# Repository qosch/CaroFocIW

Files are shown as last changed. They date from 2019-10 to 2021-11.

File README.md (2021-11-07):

# CaroFocIW
A small form factor servo inverter for BLDC motors to be mounted directly to the back of the corresponding motor. Intended use in the autonomous 1:10 scale vehicle Carolinchen XI of the Team CDLC (https://www.team-cdlc.de/, german). Firmware compatible with VESC and the custom firmware of the previous iteration. This repository only contains the hardware design.

## Features:
* Field oriented control with sine commutation
* 3× in phase current measurement with oversampling
* 14bit position encoder
* 16kHz sampling rate and PWM frequency
* JST-GH connector with supply and CAN bus interface

## Main components:
Function | used part
------------ | -------------
Microcontroller | STM32F405RGT6
Gate Driver | TLE7185-1E
Current Sensors | 3× ACS71240KEXBLT-010B3
Encoder | AS5048A
CAN Transceiver | TCAN332
Voltage Regulator | LMR16006YQ3
Power MOSFETs | 6× BSZ013NE2LS5I

## Renderings:

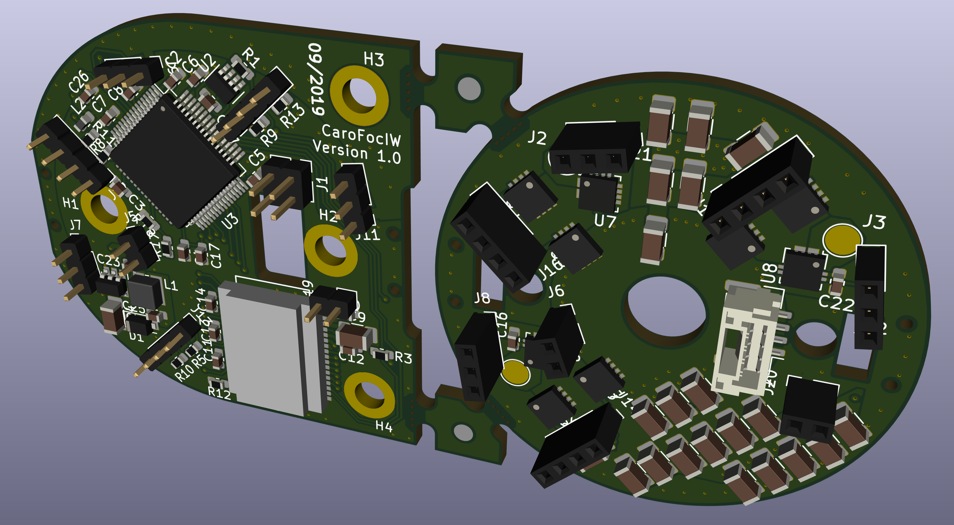
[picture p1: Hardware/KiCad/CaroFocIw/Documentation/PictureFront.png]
PCB Rendering Front


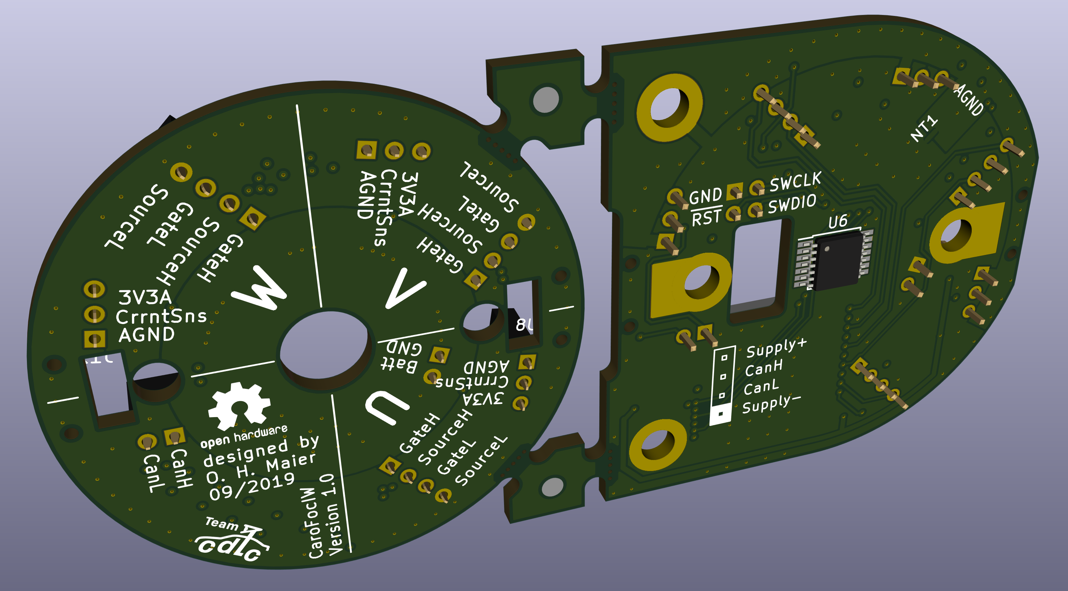
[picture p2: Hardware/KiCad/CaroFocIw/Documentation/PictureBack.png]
PCB Rendering Back


## Progress:
* [x] Schematics finished
* [x] Layout finished
* [x] PCB fabricated
* [x] PCB assembled
* [ ] Mechanical assembly finished
* [x] Basic functional tests done
  * [x] Microcontroller working
  * [x] Gate driver working
  * [x] Current sensors working
  * [x] CAN interface working
  * [x] DC link voltage measurement working
  * [x] Angle encoder working
* [x] Fully operational
* [ ] Tested on vehicle
* [ ] Long term real world testing

Link to [Schematics](https://raw.githubusercontent.com/qosch/CaroFocIW/master/Hardware/KiCad/CaroFocIw/Documentation/Schematics.pdf)

Link to [Interactive BOM](http://htmlpreview.github.io/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)

Link to [PCB assembly and test instructions](https://github.com/qosch/CaroFocIW/blob/master/Hardware/KiCad/CaroFocIw/Documentation/PcbAssemblyAndBasicTests.md)

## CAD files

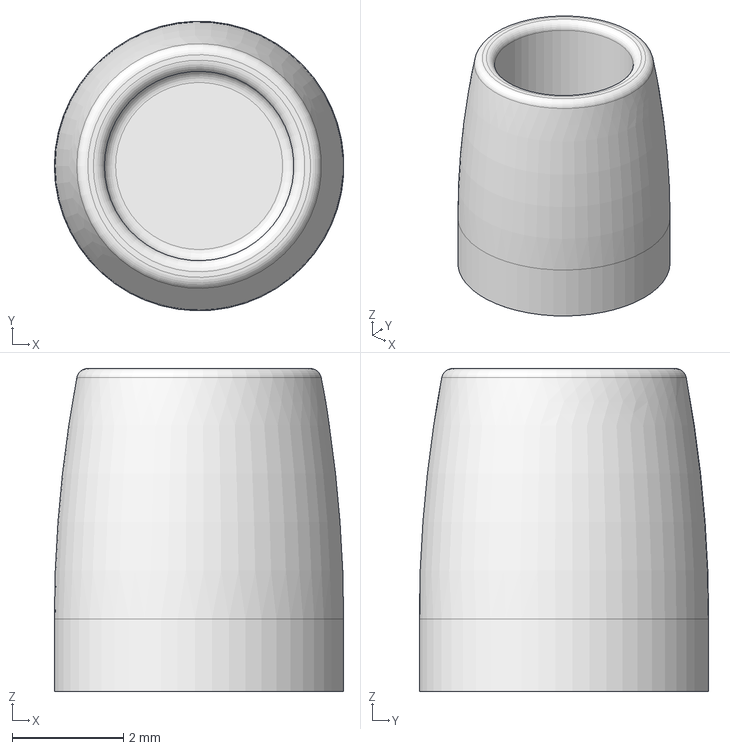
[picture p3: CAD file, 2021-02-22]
Hardware/MCAD/FreeCAD/MagnetHolderD3.4L4.5.FCStd
5.20 x 5.20 x 5.80 mm

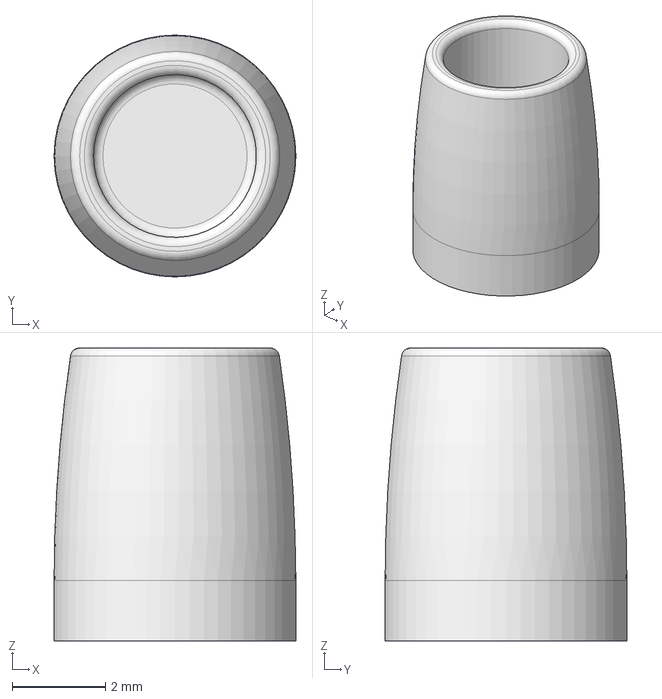
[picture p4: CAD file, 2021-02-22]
Hardware/MCAD/FreeCAD/MagnetHolderD3.5L5.0.FCStd
5.20 x 5.20 x 6.30 mm

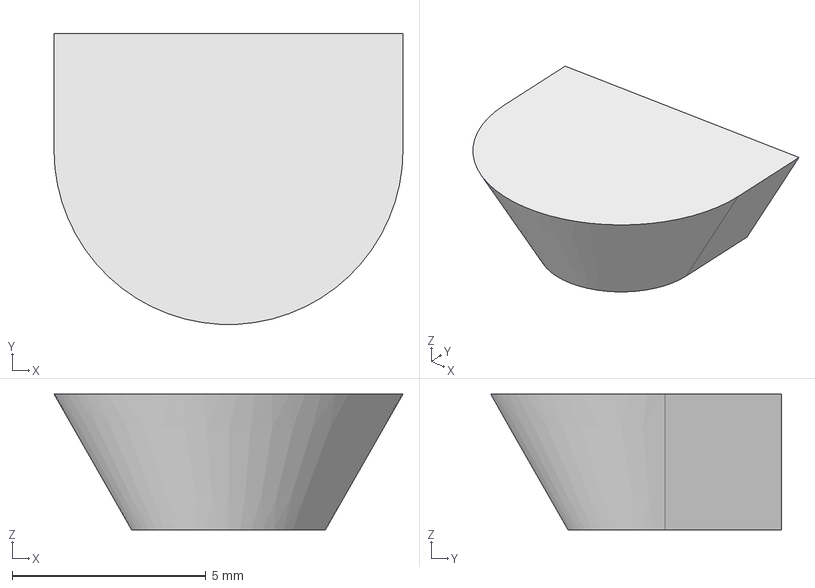
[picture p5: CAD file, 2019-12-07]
Hardware/MCAD/FreeCAD/BallHeadHolder.FCStd
9.00 x 7.49 x 3.50 mm

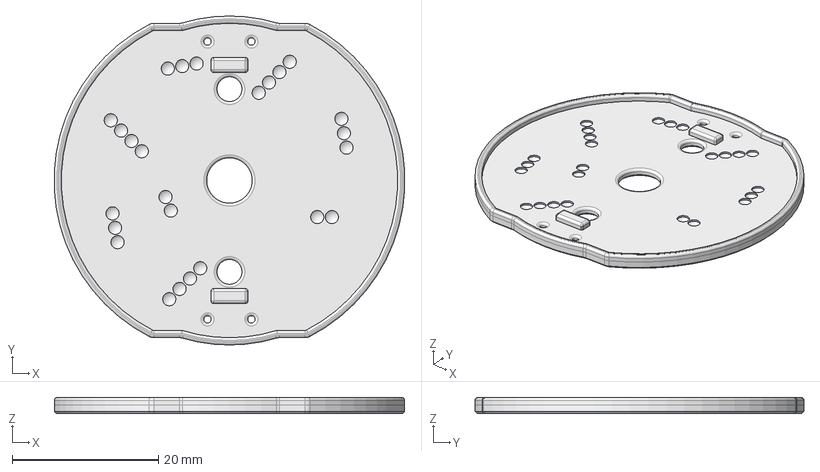
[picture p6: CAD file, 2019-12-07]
Hardware/MCAD/FreeCAD/BackPlateMotor.FCStd
47.9 x 45.0 x 2.20 mm

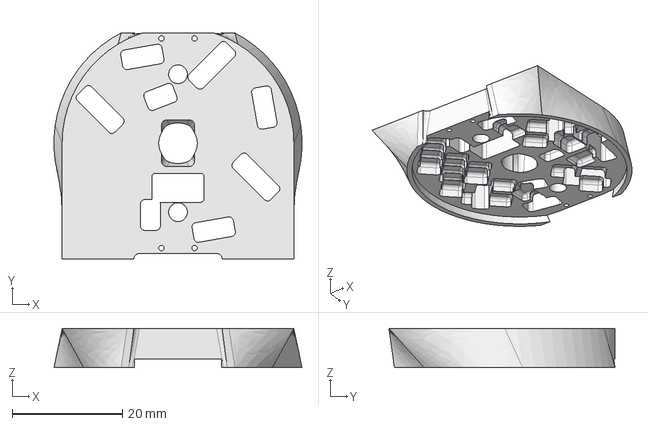
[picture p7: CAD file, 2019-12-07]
Hardware/MCAD/FreeCAD/SpacerPart.FCStd
45.0 x 41.0 x 7.10 mm

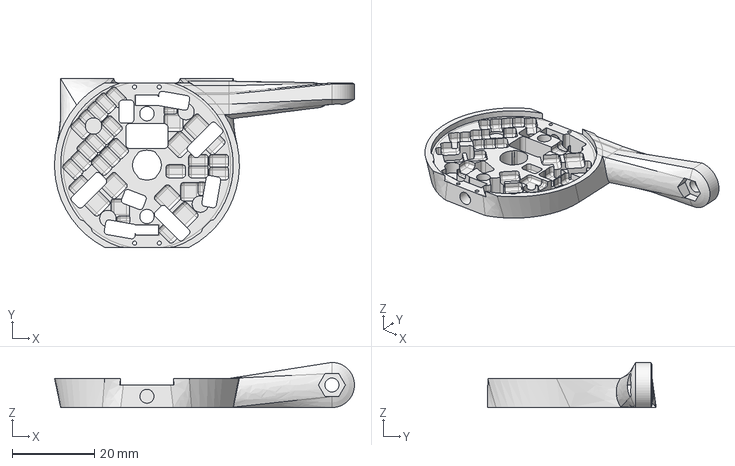
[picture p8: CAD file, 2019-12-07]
Hardware/MCAD/FreeCAD/AnotherTry.FCStd
73.0 x 41.0 x 11.0 mm

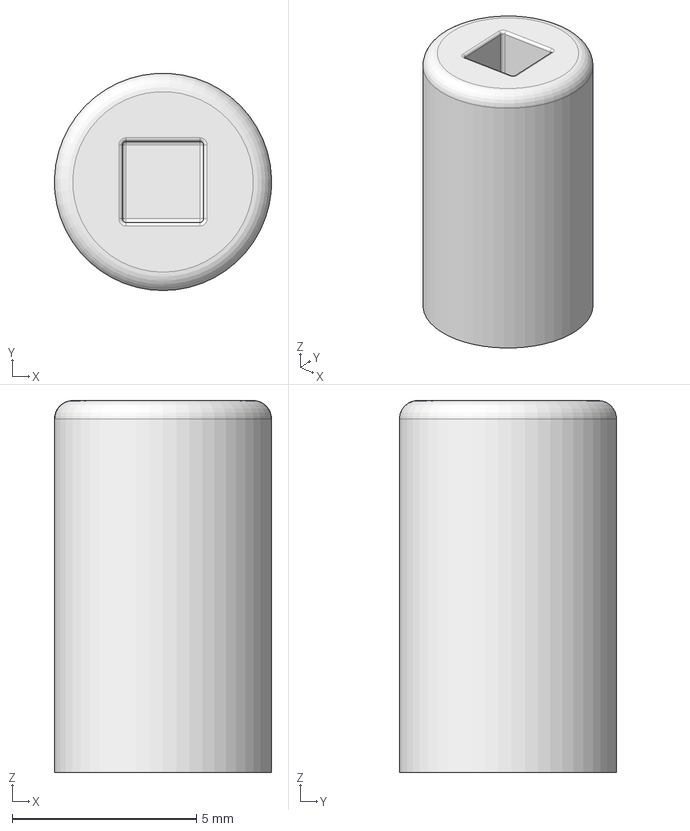
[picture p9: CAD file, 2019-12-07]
Hardware/MCAD/FreeCAD/MagnetHolderCube.FCStd
5.90 x 5.89 x 10.1 mm

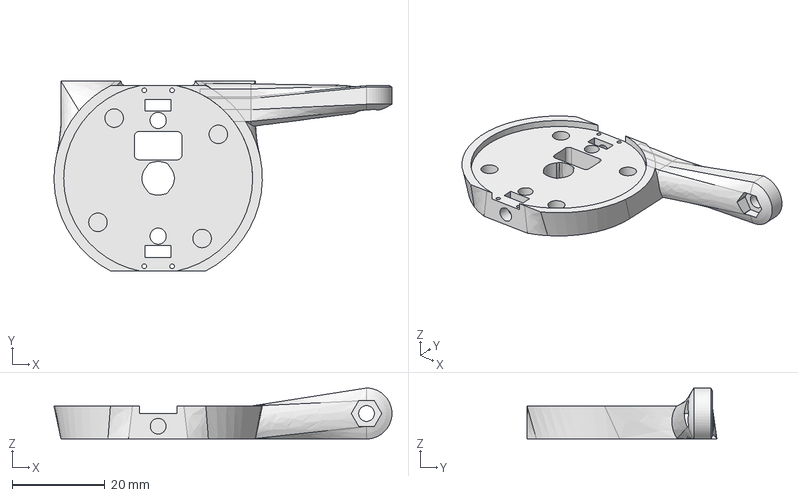
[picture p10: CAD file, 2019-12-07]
Hardware/MCAD/FreeCAD/AnotherTryPCB.FCStd
73.0 x 41.0 x 11.0 mm

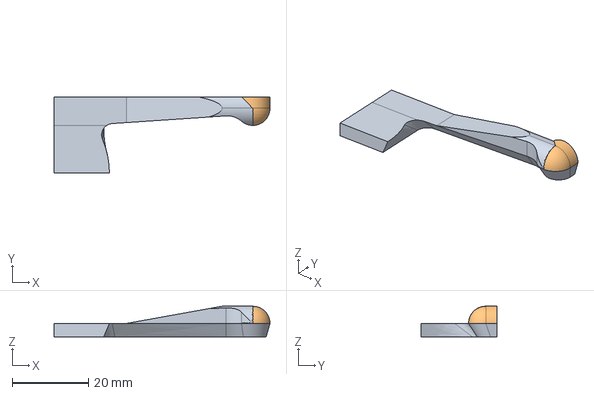
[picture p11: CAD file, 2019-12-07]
Hardware/MCAD/FreeCAD/Spurhebel.FCStd
56.5 x 20.0 x 8.00 mm

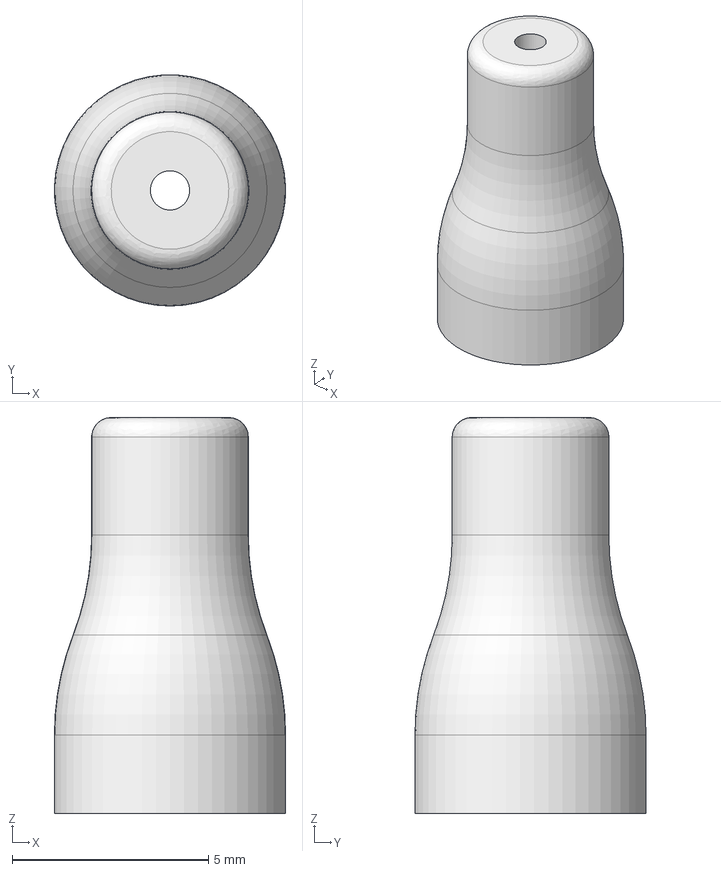
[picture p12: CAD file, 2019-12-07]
Hardware/MCAD/FreeCAD/MagnetHolderRound.FCStd
5.90 x 5.89 x 10.1 mm

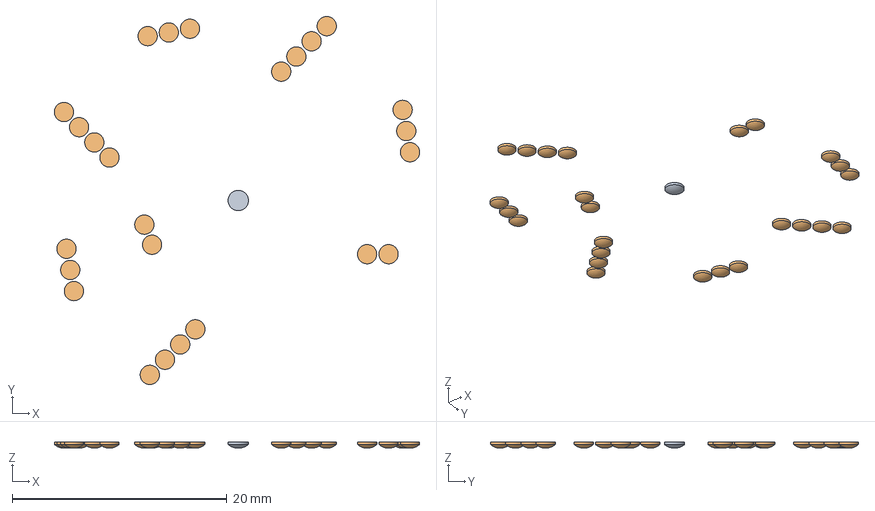
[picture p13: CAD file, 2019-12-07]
Hardware/MCAD/FreeCAD/BackPlateMotorDraft.FCStd
34.0 x 34.3 x 0.6 mm
PointArray

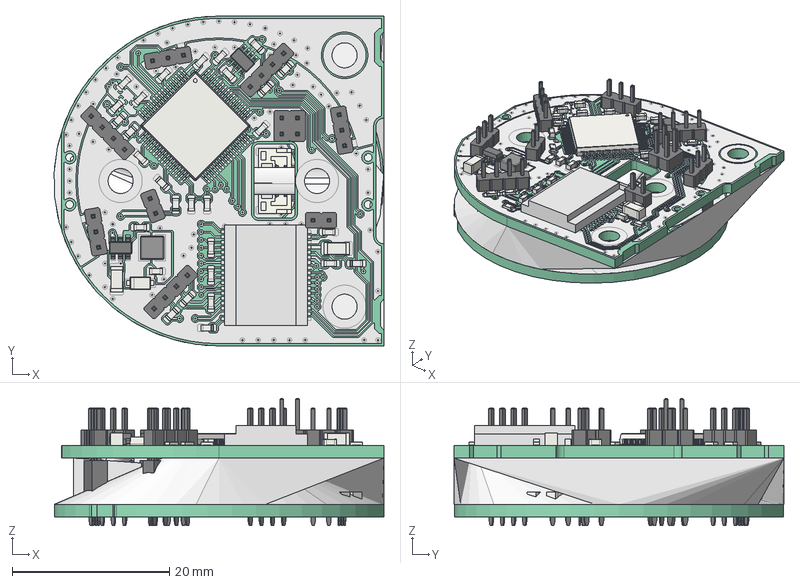
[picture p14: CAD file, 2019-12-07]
Hardware/MCAD/FreeCAD/CaroFocIw.FCStd
42.0 x 42.0 x 16.2 mm
Pcb
topTracks
botTracks
J19_PinHeader_1x02_P200mm_Vertical_5D8CF6D8
J17_PinHeader_1x04_P200mm_Vertical_5D8CF2C3
J15_PinHeader_1x04_P200mm_Vertical_5D8CF1DC
J13_PinHeader_1x04_P200mm_Vertical_5D8CE9C3
J11_PinHeader_1x03_P200mm_Vertical_5D8CF3F4
J9_PinHeader_1x03_P200mm_Vertical_5D8CF220
J7_PinHeader_1x03_P200mm_Vertical_5D8CF658
J5_PinHeader_1x02_P200mm_Vertical_5D8CF699
C4_C_0603_1608Metric_5D8CF1A5
C24_C_1206_3216Metric_5D8CEE63
C9_C_1206_3216Metric_5D8CF28C
U4_Bauteil2_5D8CF5EA
U9_SOT_23_6_5D8CF3B4
U3_LQFP_64_10x10mm_P05mm_5D8CF48A
C13_C_0603_1608Metric_5D8CF59E
C14_C_0603_1608Metric_5D8CF56E
C23_C_0603_1608Metric_5D8CEE93
C25_C_0603_1608Metric_5D8CEEC3
C8_C_0603_1608Metric_5D8CEDA3
C2_C_0603_1608Metric_5D8CEDD3
C3_C_0603_1608Metric_5D8CED43
C6_C_0603_1608Metric_5D8CEE03
C7_C_0603_1608Metric_5D8CEEF3
C12_C_0603_1608Metric_5D8CEC83
C17_C_0603_1608Metric_5D8CEF23
C11_C_0603_1608Metric_5D8CED73
R17_R_0603_1608Metric_5D96668D
R18_R_0603_1608Metric_5D8CECE3
L2_L_0603_1608Metric_5D8CF301
C26_C_0603_1608Metric_5D8CF331
C1_C_0603_1608Metric_5D8CF361
C10_C_0603_1608Metric_5D8CF25C
J1_PinHeader_2x02_P200mm_Vertical_5D8CEA0A
D1_D_SOD_123F_5D8CEFEB
R1_R_0603_1608Metric_5D8CEF53
R3_R_0603_1608Metric_5D8CEFB3
R5_R_0603_1608Metric_5D8CF08B
R8_R_0603_1608Metric_5D8CF0BB
R9_R_0603_1608Metric_5D8CF11B
R10_R_0603_1608Metric_5D8CF14B
R11_R_0603_1608Metric_5D8CEF83
R13_R_0603_1608Metric_5D8CE8C6
L1_L_Wuerth_MAPI_3015_5D8CE866
U2_SOT_23_8_5D8CE8FD
C5_C_0603_1608Metric_5D8CEE33
R12_R_0603_1608Metric_5D8FD4B1
U6_TSSOP_14_44x5mm_P065mm_5D76B81A
Pcb001
topTracks001
botTracks001
J20_PinSocket_1x02_P200mm_Vertical_5C70101C
J18_PinSocket_1x04_P200mm_Vertical_5C6EB429
J16_PinSocket_1x04_P200mm_Vertical_5C6EB411
J14_PinSocket_1x04_P200mm_Vertical_5C6ED233
J12_PinSocket_1x03_P200mm_Vertical_5D752D2D
J10_PinSocket_1x03_P200mm_Vertical_5C705940
J8_PinSocket_1x03_P200mm_Vertical_5C7059AF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

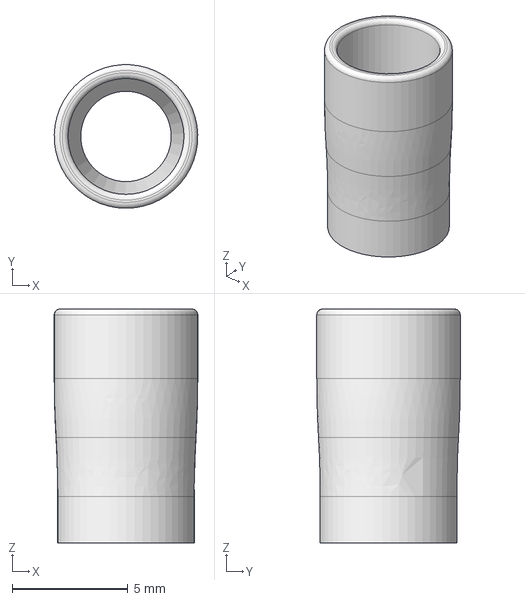
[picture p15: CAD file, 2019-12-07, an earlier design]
Hardware/MCAD/FreeCAD/MagnetHolderOld.FCStd
6.20 x 6.19 x 10.1 mm

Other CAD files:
Hardware/MCAD/FreeCAD/MagnetHolderD3.6L5.5.FCStd

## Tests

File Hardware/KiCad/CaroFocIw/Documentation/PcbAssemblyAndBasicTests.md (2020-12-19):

# Instructions for PCB assembly and tests:

1. Assemble SMT components on top side using a reflow oven.
    1. Make sure you have all neccessary components for the reflow process (go through the BOM), the process cannot be interrupted and resumed later.
    1. Apply solder paste using stencil
    1. Place all SMT components, make sure to align pin 1 correctly for ICs and polarized components. Remerks concerning individual parts:
       1. R1 is the CAN bus termination and only needs to be placed for bus participants close to each end for a linear bus (see [this link](https://www.ni.com/en-us/innovations/white-papers/09/can-physical-layer-and-termination-guide.html) for details, for example).
       1. U3 (STM32 microcontroller) has multiple dots that look like pin 1 markings. The correct one is the smaller one of the two. It is the lower left corner of the package when rotated such that the device marking text can be read.
       1. Q1-Q6 special care should be taken that enough solder paste is present at the gate pin (pin 2).
       1. J4 can be reflow soldered without issues.
    1. Reflow.
    1. Manual inspection and rework. The procedure in the next step will only find the most glaring soldering issues. It is important that most bugs are found before that by manual optical inspection and fixed afterwards.
1. Check for most common soldering issues using a multimeter:
    1. PCB A
       1. tbc
    1. PCB B
       1. J14, J16, J18: Measure capacitance between all neighbouring pins (so 9 measurements in total). Expected result: 1nF-5nF
       1. J8, J10, J12: Measure resistance between pin 1 and pin 2 and between pin 2 and pin 3. Expected result: 100kΩ-1MΩ
       1. J8, J10, J12: Measure resistance between pin 1 and pin 3. Expected result: 20kΩ-200kΩ
       1. J8, J10, J12: Measure resistance between pin 1 and pin 3. Expected result: 20kΩ-200kΩ
       1. All pins of J8, J10, J12 should have a resistance >10MΩ to any pin of any other connector on this PCB (except for the pins of the same connector). Check J8<->J14+J6, J10<->J16+J6, J12<->J18+J6.
       1. Pin 1 and 2 of J20 should only have connection to pins 2 and 3 of J4. Check J20<->J6 (all 4 combinations). Expected result: >10MΩ
       1. J6: Measure capacitance between pin 1 and pin 4. Expected result: 150-250µF
1. Apply power to the individual PCBs.
   1. PCB A: GND -> J5 Pin 1, +3.3V -> J7/J9/J11 pin 3. Set current limit to 50mA and measure supply current. If you want to be extra careful use a 10Ω series resistor. Turn up voltage slowly. With unprogrammed microcontroller suppy current should remain <20mA.
   1. PCB A: GND -> J5 pin 1, +20V -> J5 pin 2. Set current limit to 100mA and measure supply current as well as voltage at J7/J9/J11 pin 3. Turn up voltage slowly. Voltage at J7/J9/J11 pin 3 should remain at 3.2-3.4V as soon as power supply voltage reaches 3.5V. Suppy current should remain <200mA
   1. PCB B: GND -> J6 pin 1 or J4 pin 1, +20V -> J6 Pin 2 or J4 pin 4. Set current limit to 50mA and measure supply current. If you want to be extra careful use a 1kΩ series resistor. Turn up voltage slowly. Suppy current should remain <20mA.
   1. PCB B: Repeat for J8, J10, J12: GND -> pin 1, +3.3V pin 3. Set current limit to 50mA. If you want to be extra careful use a 10Ω series resistor. Turn up voltage slowly. Suppy current should remain <20mA. Measure voltage between pin 1 (GND) and pin 2. Expected voltage: half the supply voltage at pin 3.
1. Solder in U6 using hot air, infrared or soldering iron. Manual inspection and rework. Use a continuity tester to check all pins against GND (J5 pin 1), only pin 13 should be connected. Check all pins against +3.3V (J7/J9/J11 pin 3), only pin 11 and 12 should be connected. Check that pin 1-4 do not have shorts to neighbours. Repeat "Apply power" tests with PCB A.
1. Break apart PCB A and PCB B. The intermediate parts are not needed anymore.
1. Assemble the inter-board-connectors. They are used a bit differently than normal and need to be modified.
   1. Break of parts of the male pin header connector to the neccessary leghts (2× 2 pin, 3× 3 pin, 3x 4 pin).
   1. The black plastic part is not in the right position for our usage, it needs to be pushed down such that the longer part of the pin sticks out even longer. To do that, place an unpopulated PCB on a flat, hard surface, put the shorter side of a pinheader in to the holes and push the plastic down to the PCB.
   1. Insert all modified pin headers into PCB A so that the black plastic part and the very short side of the pins is on the top side.
   1. Put an unpopulated PCB on top so that the pinheaders are held in place when you turn the PCB around.
   1. Solder the connectors in from the bottom side. Use as little solder as possible, only make sure the hole around the pin is filled with solder all around the pin. Try to prevent the solder from flowing up the pin or leaving solder on the upper part of the pin as it will prevent the pin from being fully inserted into the female part on PCB B.
   1. Insert the female headers from the top side of PCB B and solder them from the back. Again, try to use as little solder as possible.
   1. Cut the pins on the back of PCB B as short as possible to prevent them from being shorted by the motor's metal case. Make sure no cut off metal parts remain on the PCBs.
1. Assemble programming connector J1 from top, solder from back.
1. Wash PCB A and B to remove remaining flux.
1. Plug PCB A into PCB B and apply power to J6 pin 1 (GND) and pin 4 (+20V). With unprogrammed microcontroller, suppy current should remain <50mA.
1. Connect a programmer to J1 and check connection to the microcontroller using the tool of you choice.
Additional remark: Be very careful when unplugging PCB A from PCB B. The inter-board connectors may break when PCBs are not kept parallel during unplugging.

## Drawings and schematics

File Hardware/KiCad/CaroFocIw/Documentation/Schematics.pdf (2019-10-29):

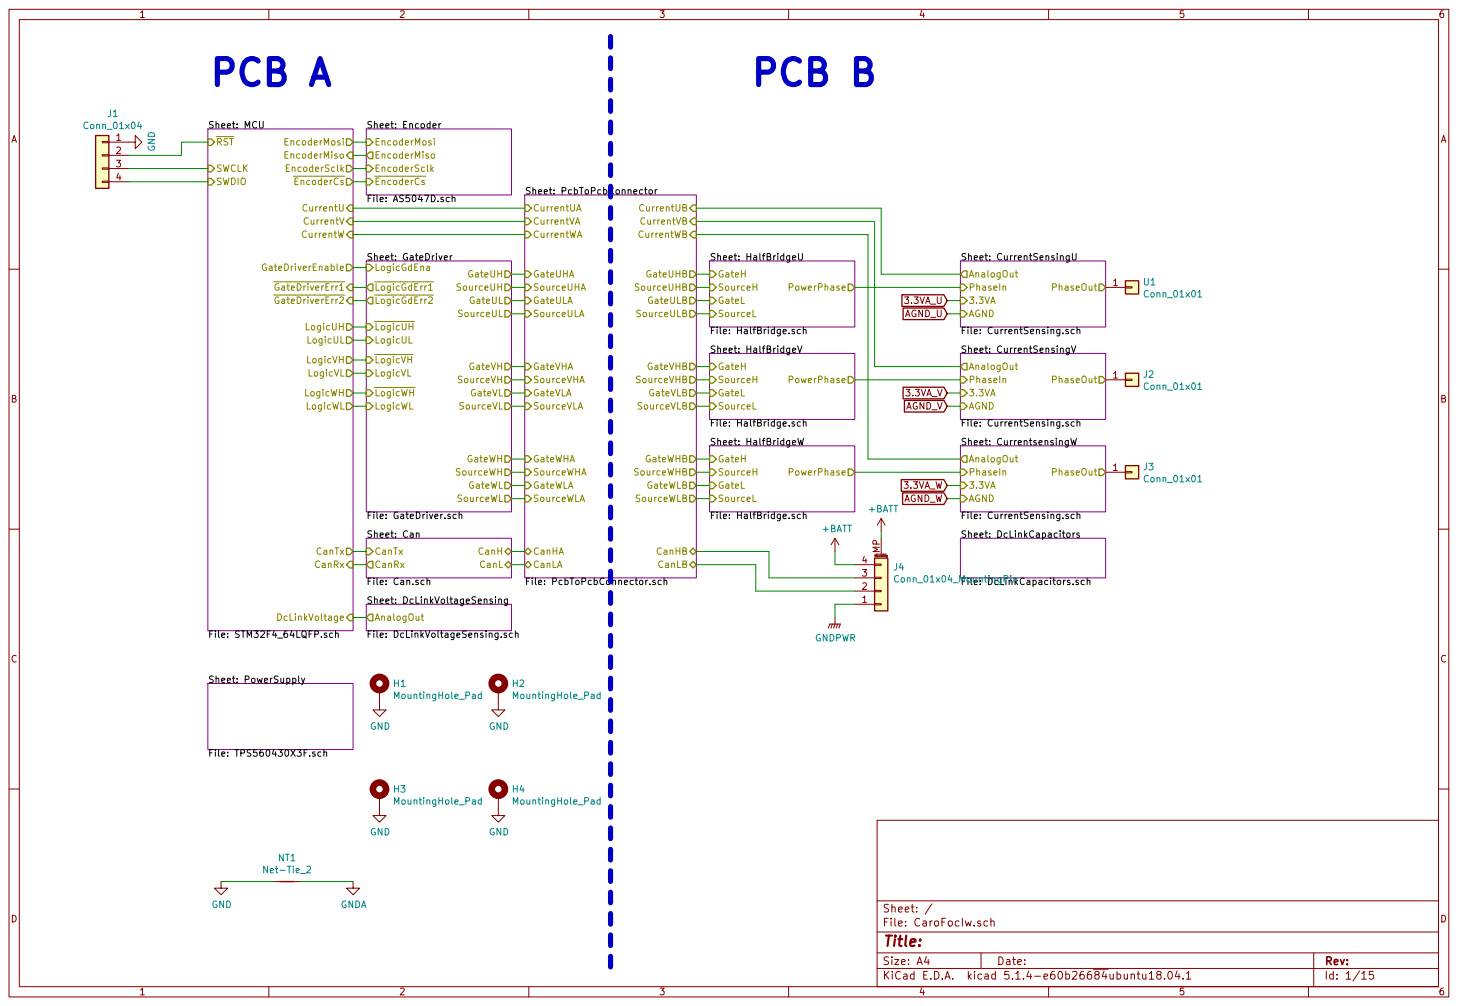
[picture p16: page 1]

LogicWL EncoderSclk EncoderMiso EncoderMosi EncoderCs GateDriverEnable GateDriverErr1 GateDriverErr2 SWDIO
File: STM32F4_64LQFP.schCanRx CanTx CurrentU

Sheet: HalfBridgeU
File: HalfBridge.sch PowerPhase GateH GateL SourceL SourceH

LogicGdEna
SourceUL SourceVL SourceWL GateWL GateVL GateUL GateWH GateVH GateUH

Sheet: HalfBridgeV

Id: 1/15 Title: File: CaroFocIw.sch Sheet: / Sheet: DcLinkVoltageSensing
AnalogOut
File: DcLinkVoltageSensing.sch

Sheet: PowerSupply File: TPS560430X3F.sch

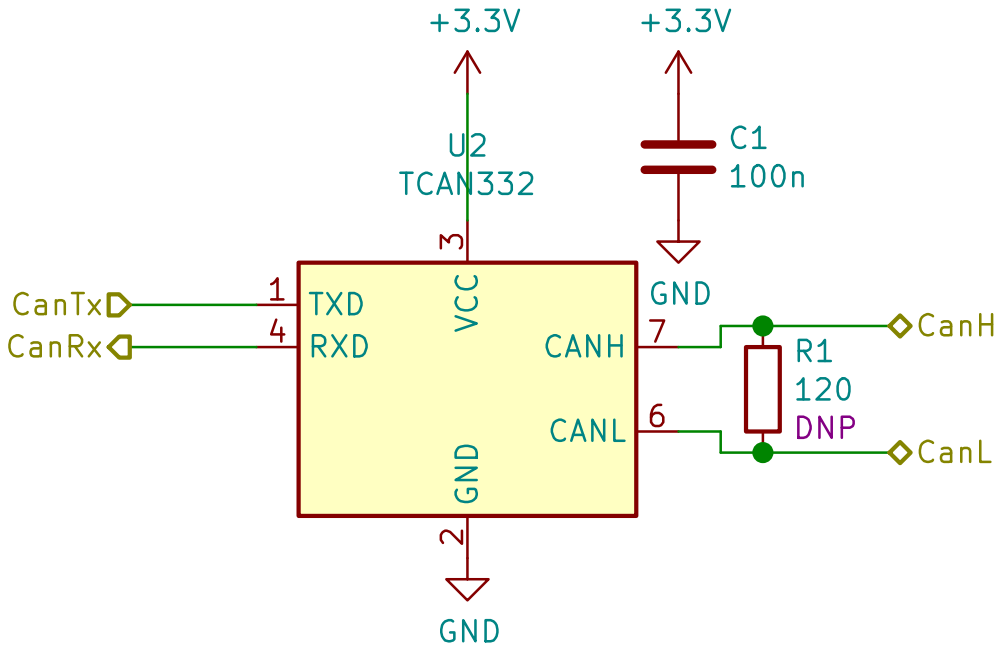
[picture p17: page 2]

3 RXD 4 CANL 6 CANH 7 U2 TCAN332 CanRx CanL CanH CanTx

Id: 2/15 Title: File: Can.sch Sheet: /Can/ R1

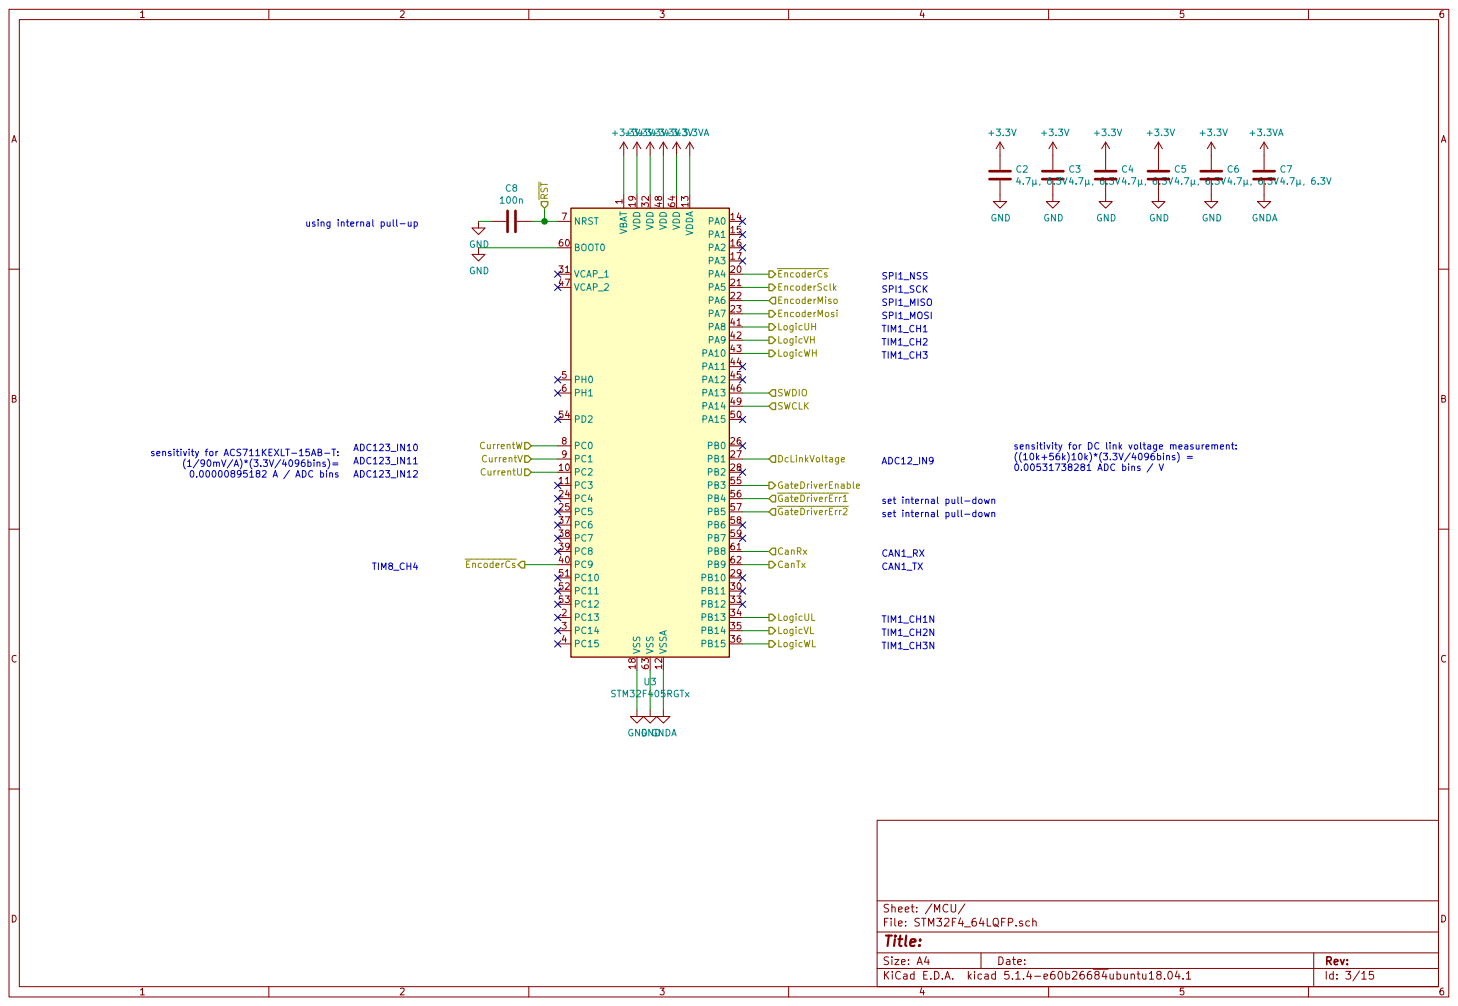
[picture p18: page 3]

1 VCAP_1 31 VCAP_2 47 VDD 19 VDD 32 VDD 48 VDD 64 VDDA 13 VSS 18 VSS 63 VSSA 12 U3 STM32F405RGTx

using internal pull-up

CanTx GateDriverErr2 EncoderCs EncoderMosi EncoderMiso ADC123_IN12 TIM8_CH4

LogicWL EncoderSclk GateDriverEnable CurrentU

sensitivity for DC link voltage measurement:
((10k+56k)10k)*(3.3V/4096bins) =
0.00531738281 ADC bins / V

set internal pull-down
set internal pull-down TIM1_CH1N

File: STM32F4_64LQFP.sch Sheet: /MCU/
Id: 3/15 Title:

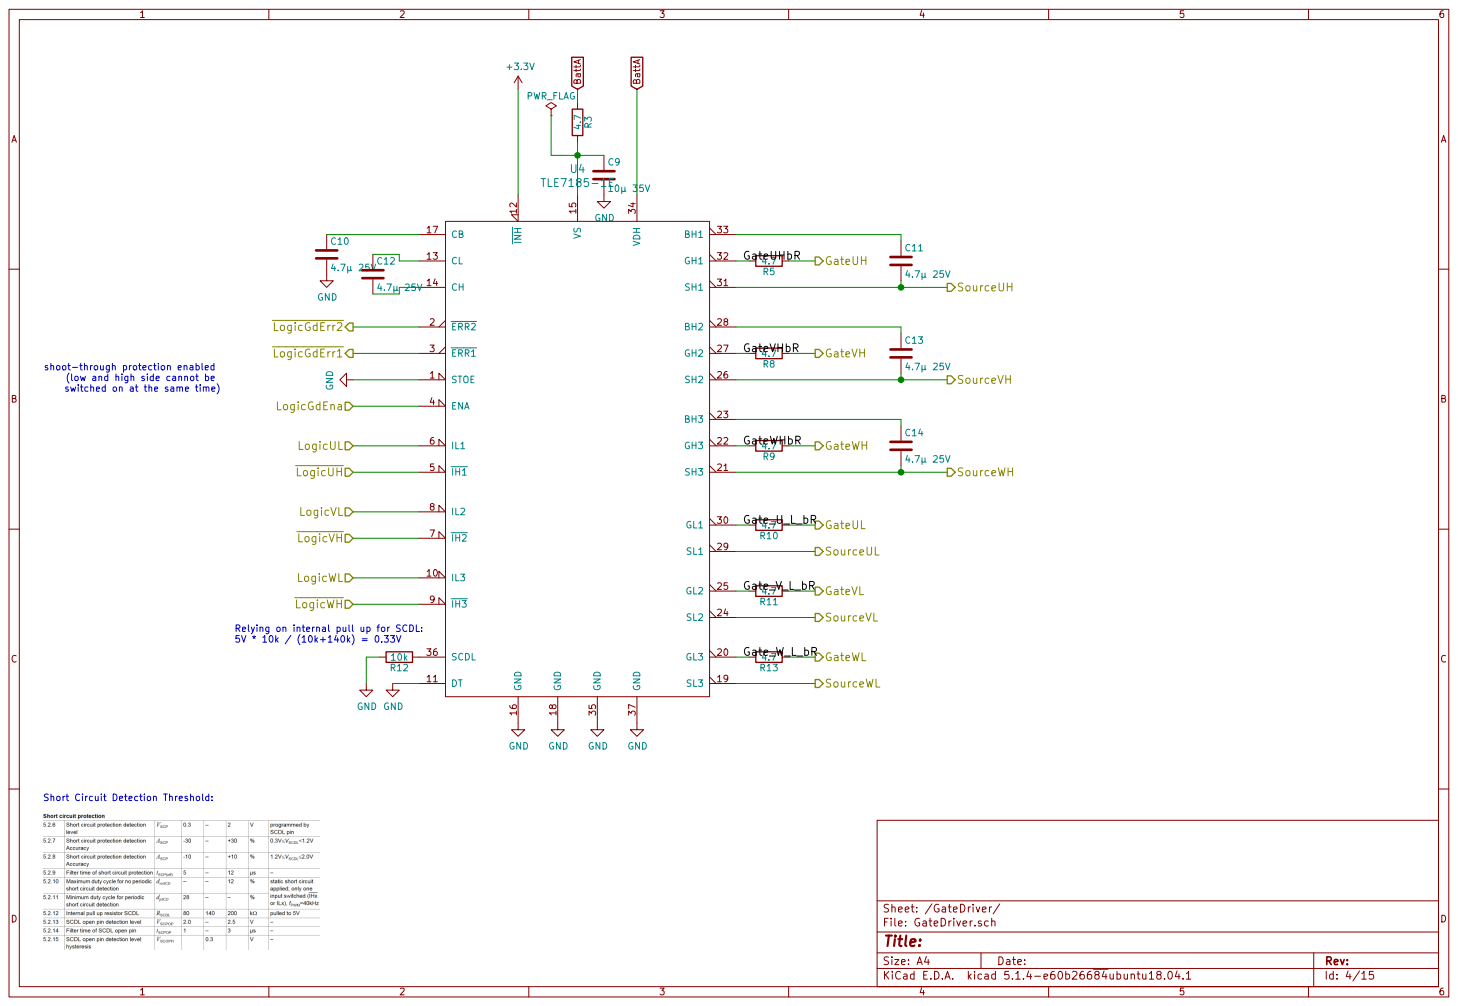
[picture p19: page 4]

shoot-through protection enabled
(low and high side cannot be
switched on at the same time)

Relying on internal pull up for SCDL:

Id: 4/15 Title: File: GateDriver.sch Sheet: /GateDriver/ R12

Short Circuit Detection Threshold:

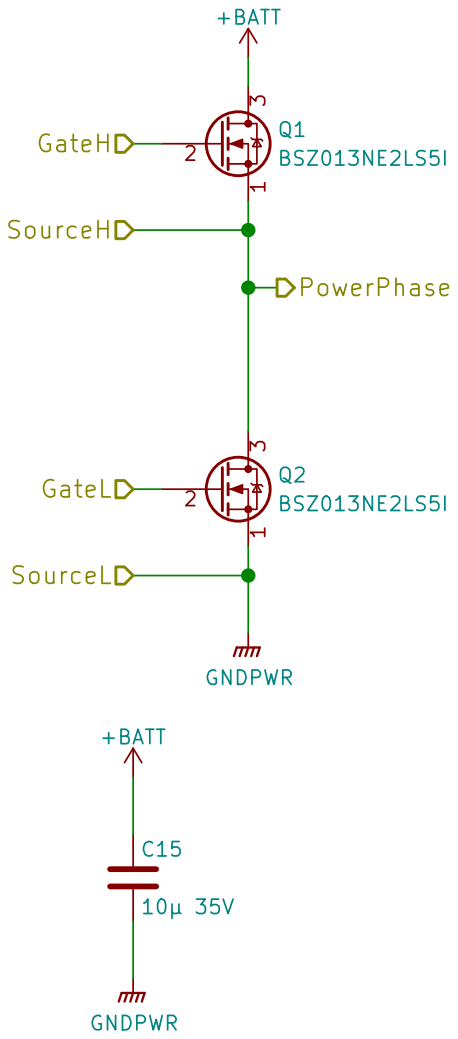
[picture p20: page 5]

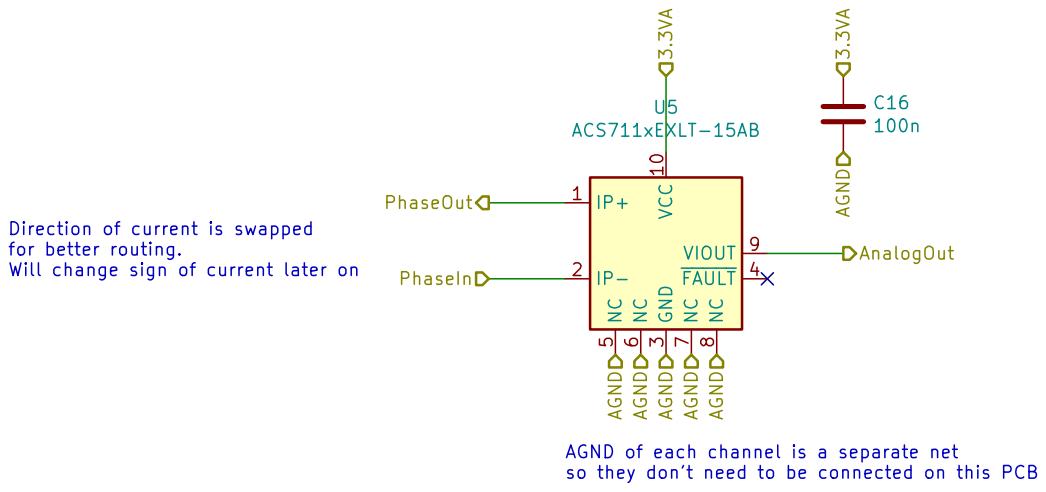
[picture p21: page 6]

AnalogOut PhaseIn Direction of current is swapped
for better routing.
Will change sign of current later on

AGND of each channel is a separate net
so they don't need to be connected on this PCB

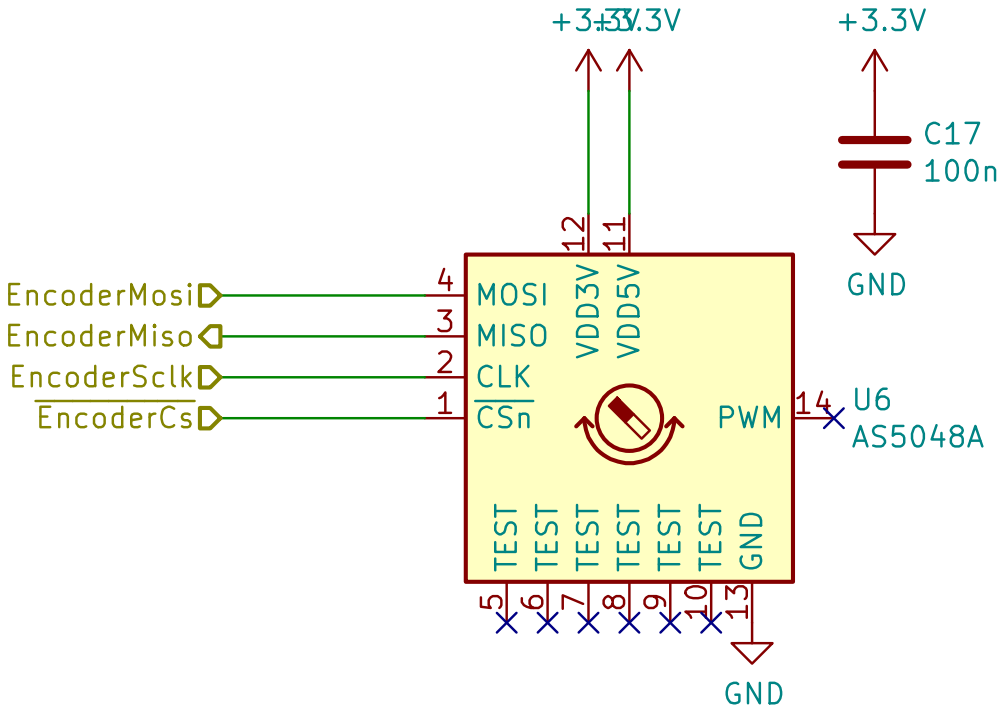
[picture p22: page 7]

100n EncoderMosi EncoderCs EncoderSclk EncoderMiso

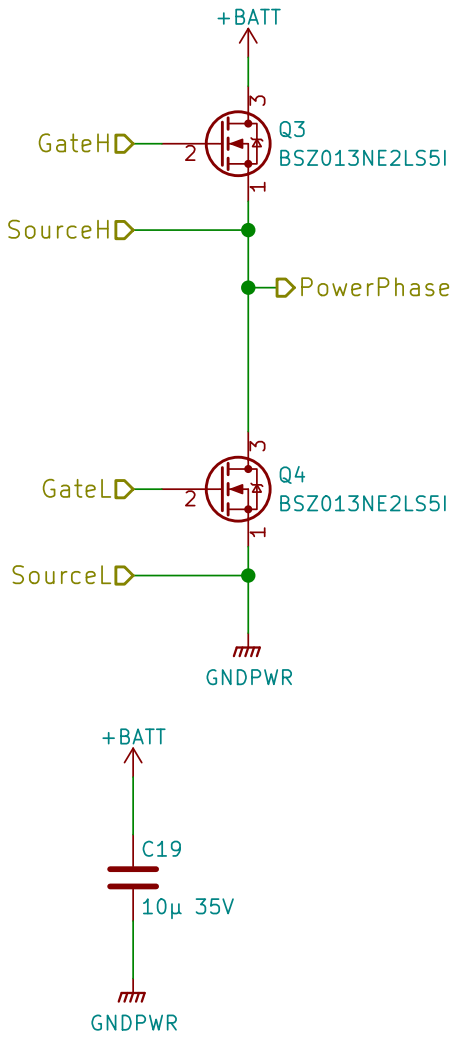
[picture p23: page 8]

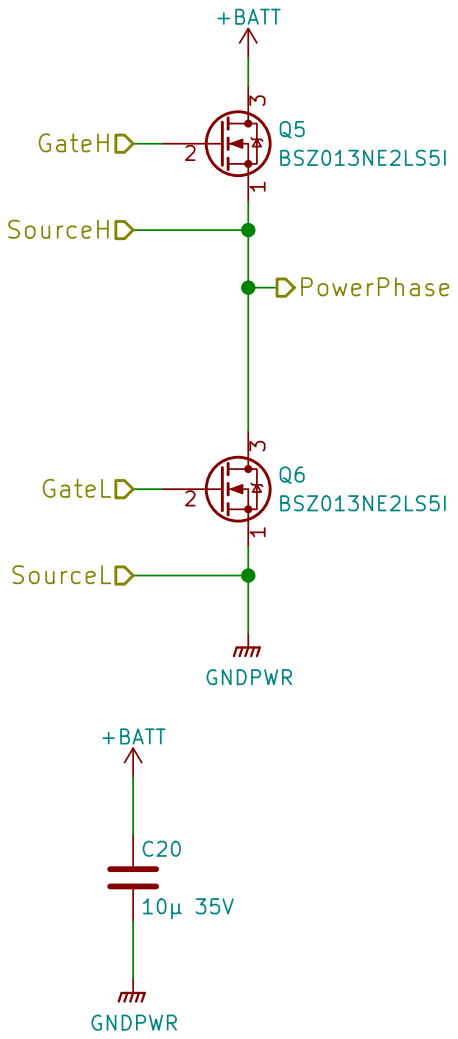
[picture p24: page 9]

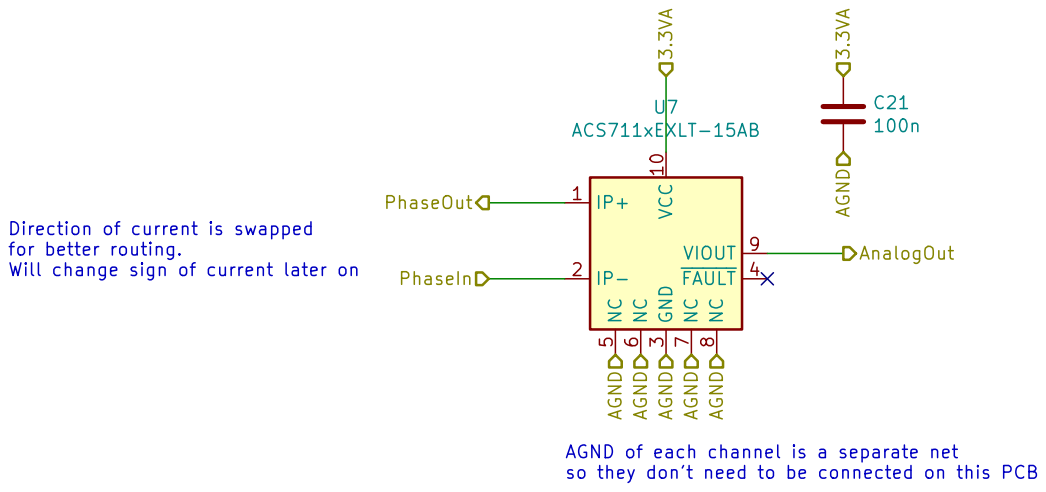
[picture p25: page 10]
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

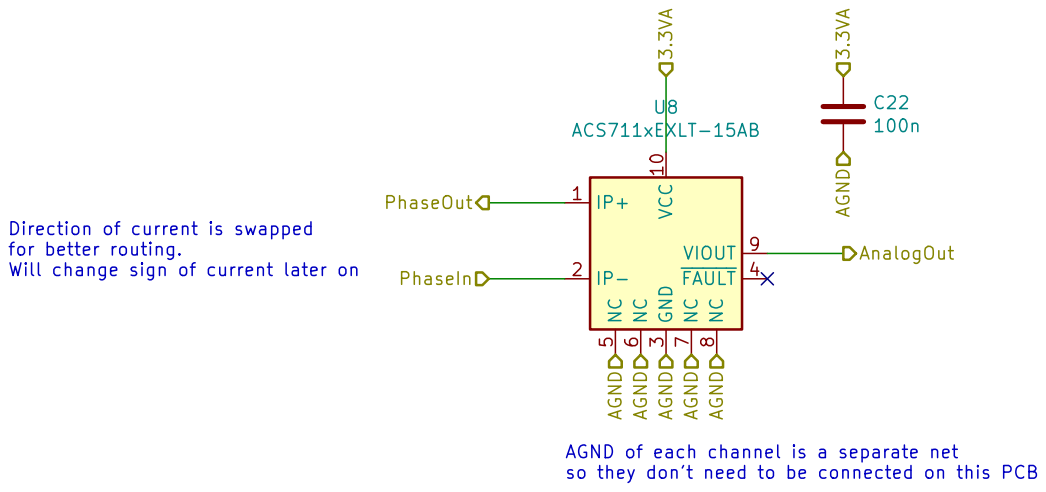
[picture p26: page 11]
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

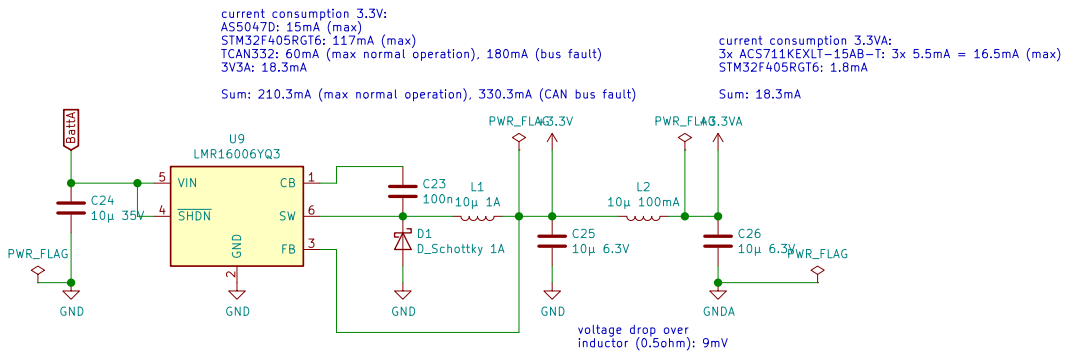
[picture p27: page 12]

current consumption 3.3V:
AS5047D: 15mA (max)
STM32F405RGT6: 117mA (max)
TCAN332: 60mA (max normal operation), 180mA (bus fault) 3V3A: 18.3mA

Sum: 210.3mA (max normal operation), 330.3mA (CAN bus fault)

2 FB 3 SHDN 4 VIN 5 SW 6 U9

Id: 12/15 Title: File: TPS560430X3F.sch Sheet: /PowerSupply/


+BATT GNDPWR GNDA GNDA GNDA

AGND and 3.3VA of each channel don't need to be connected on PCB B

(they are connected on PCB A)

Id: 13/15 Title: File: PcbToPcbConnector.sch Sheet: /PcbToPcbConnector/


outputs 3.3V for 21.78V Battery voltage



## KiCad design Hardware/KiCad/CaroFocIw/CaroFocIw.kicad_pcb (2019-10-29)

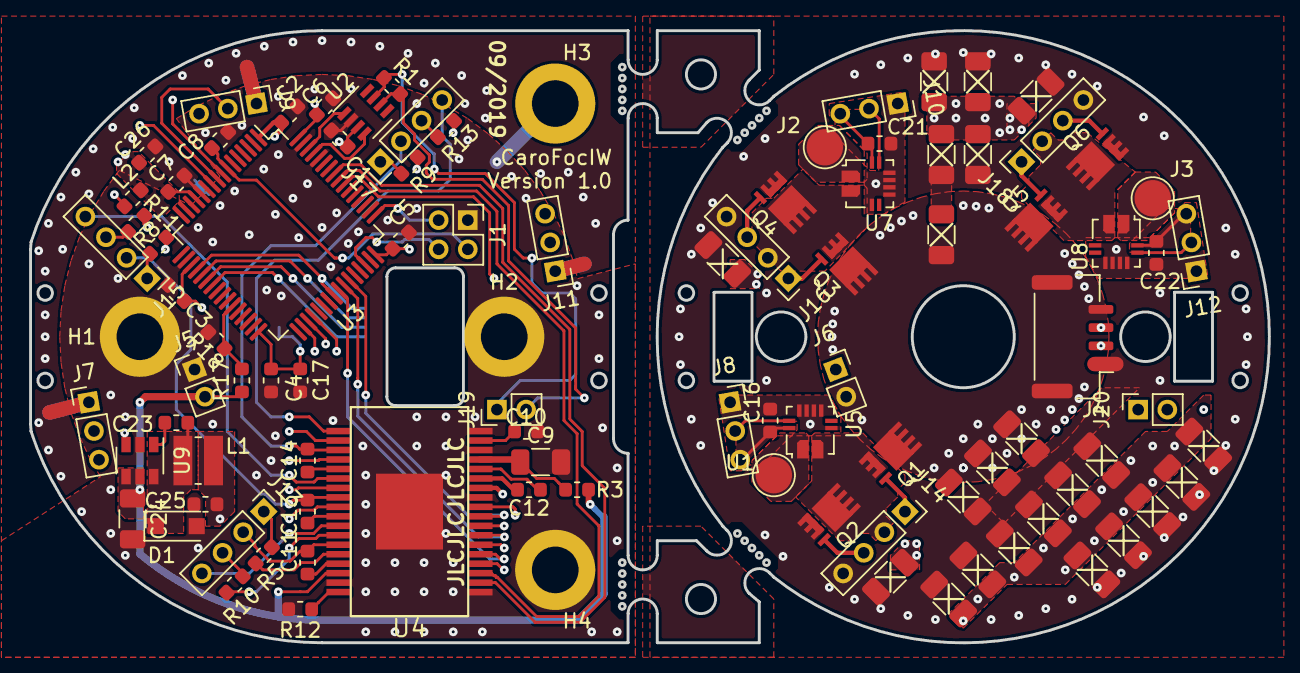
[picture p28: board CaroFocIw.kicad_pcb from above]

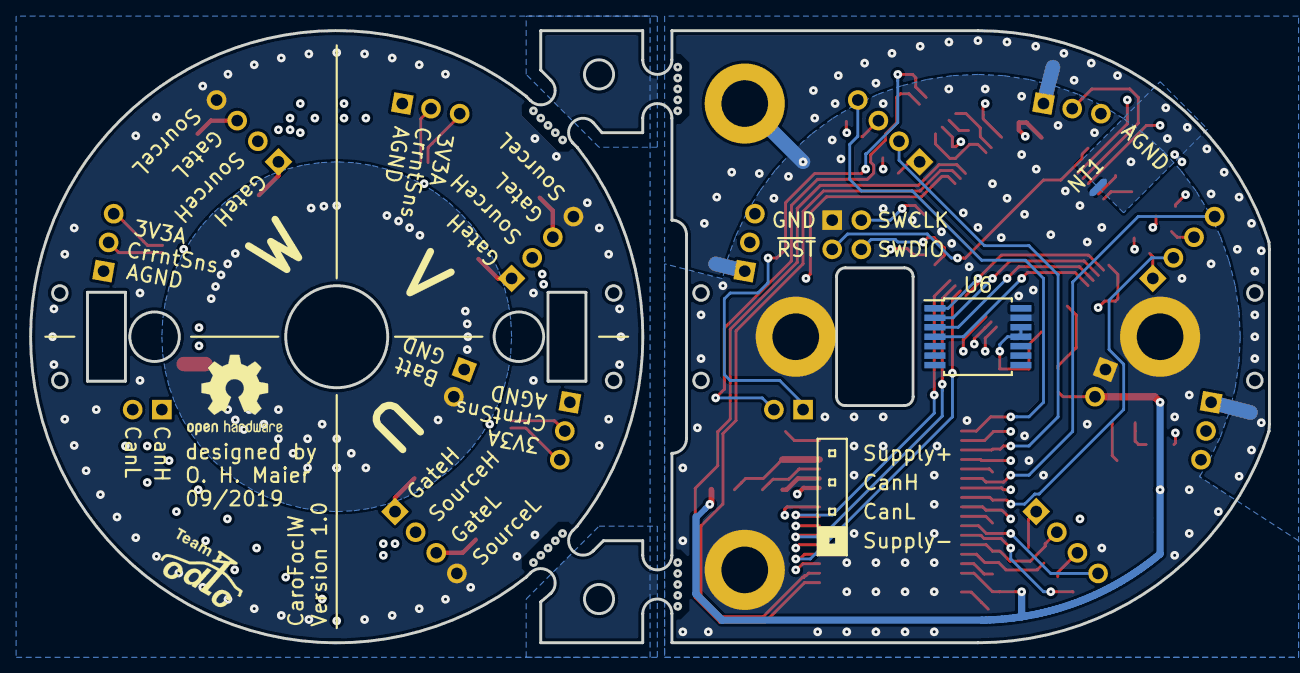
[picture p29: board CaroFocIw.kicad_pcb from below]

Board: 4 copper layers, 85.0 x 42.0 mm, 98 parts (2 on the bottom side), 82 nets.

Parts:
C1, C8, C16, C17, C21, C22, C23: 100n; C_0603_1608Metric
C2, C3, C4, C5, C6, C7: 4.7µ, 6.3V; C_0603_1608Metric
C9, C27, C28, C29, C30, C31, C32, C33, C34, C35, C36, C37, C38, C39, C40, C41, C42, C43, C44, C45: 10µ 35V; C_1206_3216Metric
C10, C11, C12, C13, C14: 4.7µ 25V; C_0603_1608Metric
C15, C19, C20, C24: 10μ 35V; C_1206_3216Metric
C25, C26: 10μ 6.3V; C_0603_1608Metric
D1: D_Schottky 1A; D_SOD-123F
H1, H2, H3, H4: MountingHole_Pad; MountingHole_3.2mm_M3_ISO14580_Pad
J1: Conn_01x04; PinHeader_2x02_P2.00mm_Vertical
J2, J3: Conn_01x01; TestPoint_Pad_D2.5mm
J4: Conn_01x04_MountingPin; JST_GH_BM04B-GHS-TBT_1x04-1MP_P1.25mm_Vertical
J5, J19: Conn_01x02; PinHeader_1x02_P2.00mm_Vertical
J6, J20: Conn_01x02; PinSocket_1x02_P2.00mm_Vertical
J7, J9, J11: Conn_01x03; PinHeader_1x03_P2.00mm_Vertical
J8, J10, J12: Conn_01x03; PinSocket_1x03_P2.00mm_Vertical
J13, J15, J17: Conn_01x04; PinHeader_1x04_P2.00mm_Vertical
J14, J16, J18: Conn_01x04; PinSocket_1x04_P2.00mm_Vertical
L1: 10μ 1A; L_Wuerth_MAPI-3015
L2: 10μ 100mA; L_0603_1608Metric
NT1: Net-Tie_2; NetTie-2_SMD_Pad0.5mm
Q1, Q2, Q3, Q4, Q5, Q6: BSZ013NE2LS5I; PG-TSDSON-8-FL
R1: 120; R_0603_1608Metric
R3, R5, R8, R9, R10, R11, R13: 4.7; R_0603_1608Metric
R12, R18: 10k; R_0603_1608Metric
R17: 56k; R_0603_1608Metric
U1: Conn_01x01; TestPoint_Pad_D2.5mm
U2: TCAN332; SOT-23-8
U3: STM32F405RGTx; LQFP-64_10x10mm_P0.5mm
U4: TLE7185-1E; PG-DSO-36-38
U5, U7, U8: ACS711xEXLT-15AB; Allegro_QFN-12-10-1EP_3x3mm_P0.5mm
U6: AS5048A; TSSOP-14_4.4x5mm_P0.65mm
U9: LMR16006YQ3; SOT-23-6

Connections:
3.3VA_U: C16.1, J8.3, U5.10
3.3VA_V: C21.1, J10.3, U7.10
3.3VA_W: C22.1, J12.3, U8.10
+3.3VA: C7.1, C26.1, J7.3, J9.3, J11.3, L2.1, U3.13
+3V3: C1.1, C2.1, C3.1, C4.1, C5.1, C6.1, C17.1, C25.1, L1.1, L2.2, U2.3, U3.1, U3.19, U3.32, U3.48, U3.64, U4.12, U6.11, U6.12, U9.3
+BATT: C15.1, C19.1, C20.1, C27.1, C28.1, C29.1, C30.1, C31.1, C32.1, C33.1, C34.1, C35.1, C36.1, C37.1, C38.1, C39.1, C40.1, C41.1, C42.1, C43.1, C44.1, C45.1, J4.4, J4.MP, J6.2, Q1.3, Q3.3, Q5.3
/Can/CanH: J19.1, R1.1, U2.7
/Can/CanL: J19.2, R1.2, U2.6
/Can/CanRx: U2.4, U3.61
/Can/CanTx: U2.1, U3.62
/CurrentSensingU/AnalogOut: J8.2, U5.9
/CurrentSensingU/PhaseIn: J14.2, Q1.1, Q2.3, U5.2
/CurrentSensingU/PhaseOut: U1.1, U5.1
/CurrentSensingV/AnalogOut: J10.2, U7.9
/CurrentSensingV/PhaseIn: J16.2, Q3.1, Q4.3, U7.2
/CurrentSensingV/PhaseOut: J2.1, U7.1
/CurrentsensingW/AnalogOut: J12.2, U8.9
/CurrentsensingW/PhaseIn: J18.2, Q5.1, Q6.3, U8.2
/CurrentsensingW/PhaseOut: J3.1, U8.1
/DcLinkVoltageSensing/AnalogOut: R17.2, R18.1, U3.27
/Encoder/EncoderMiso: U3.22, U6.3
/Encoder/EncoderMosi: U3.23, U6.4
/Encoder/EncoderSclk: U3.21, U6.2
/Encoder/~EncoderCs: U3.20, U3.40, U6.1
/GateDriver/GateUH: J13.1, R5.1
/GateDriver/GateUHbR: R5.2, U4.32
/GateDriver/GateUL: J13.3, R10.1
/GateDriver/GateVH: J15.1, R8.1
/GateDriver/GateVHbR: R8.2, U4.27
/GateDriver/GateVL: J15.3, R11.1
/GateDriver/GateWH: J17.1, R9.1
/GateDriver/GateWHbR: R9.2, U4.22
/GateDriver/GateWL: J17.3, R13.1
/GateDriver/Gate_U_L_bR: R10.2, U4.30
/GateDriver/Gate_V_L_bR: R11.2, U4.25
/GateDriver/Gate_W_L_bR: R13.2, U4.20
/GateDriver/LogicUL: U3.34, U4.6
/GateDriver/LogicVL: U3.35, U4.8
/GateDriver/LogicWL: U3.36, U4.10
/GateDriver/SourceUH: C11.2, J13.2, U4.31
/GateDriver/SourceUL: J13.4, U4.29
/GateDriver/SourceVH: C13.2, J15.2, U4.26
/GateDriver/SourceVL: J15.4, U4.24
/GateDriver/SourceWH: C14.2, J17.2, U4.21
/GateDriver/SourceWL: J17.4, U4.19
/HalfBridgeU/GateH: J14.1, Q1.2
/HalfBridgeU/GateL: J14.3, Q2.2
/HalfBridgeV/GateH: J16.1, Q3.2
/HalfBridgeV/GateL: J16.3, Q4.2
/HalfBridgeW/GateH: J18.1, Q5.2
/HalfBridgeW/GateL: J18.3, Q6.2
/MCU/CurrentU: J7.2, U3.10
/MCU/CurrentV: J9.2, U3.9
/MCU/CurrentW: J11.2, U3.8
/MCU/GateDriverEnable: U3.55, U4.4
/MCU/LogicUH: U3.41, U4.5
/MCU/LogicVH: U3.42, U4.7
/MCU/LogicWH: U3.43, U4.9
/MCU/SWCLK: J1.3, U3.49
/MCU/SWDIO: J1.4, U3.46
/MCU/~GateDriverErr1: U3.56, U4.3
/MCU/~GateDriverErr2: U3.57, U4.2
/MCU/~RST: C8.1, J1.2, U3.7
/PcbToPcbConnector/CanHB: J4.3, J20.1
/PcbToPcbConnector/CanLB: J4.2, J20.2
AGND_U: C16.2, J8.1, U5.3, U5.5, U5.6, U5.7, U5.8
AGND_V: C21.2, J10.1, U7.3, U7.5, U7.6, U7.7, U7.8
AGND_W: C22.2, J12.1, U8.3, U8.5, U8.6, U8.7, U8.8
BattA: C24.1, J5.2, R3.1, R17.1, U4.34, U9.4, U9.5
GND: C1.2, C2.2, C3.2, C4.2, C5.2, C6.2, C8.2, C9.2, C10.2, C17.2, C24.2, C25.2, D1.2, H1.1, H2.1, H3.1, H4.1, J1.1, J5.1, NT1.1, R12.2, R18.2, U2.2, U3.18, U3.60, U3.63, U4.1, U4.11, U4.16, U4.18, U4.35, U4.37, U6.13, U9.2
GNDA: C7.2, C26.2, J7.1, J9.1, J11.1, NT1.2, U3.12
GNDPWR: C15.2, C19.2, C20.2, C27.2, C28.2, C29.2, C30.2, C31.2, C32.2, C33.2, C34.2, C35.2, C36.2, C37.2, C38.2, C39.2, C40.2, C41.2, C42.2, C43.2, C44.2, C45.2, J4.1, J6.1, J14.4, J16.4, J18.4, Q2.1, Q4.1, Q6.1
unnamed: C9.1, R3.2, U4.15
unnamed: C10.1, U4.17
unnamed: C11.1, U4.33
unnamed: C12.1, U4.13
unnamed: C12.2, U4.14
unnamed: C13.1, U4.28
unnamed: C14.1, U4.23
unnamed: C23.1, U9.1
unnamed: C23.2, D1.1, L1.2, U9.6
unnamed: R12.1, U4.36

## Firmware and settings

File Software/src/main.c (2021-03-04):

/*
 * This file is part of the CaroFoc project.
 */

#include <pins.h>
#include <timer.h>
#include <clock.h>
#include <gpio.h>
#include <pins.h>
#include <libopencm3/stm32/timer.h>
#include <libopencm3/stm32/gpio.h>
#include <libopencm3/stm32/rcc.h>

uint32_t i = 0;
int32_t testvar = 0;
uint32_t tim1_val = 0;
uint32_t tim8_val = 0;

int main(void){
    clock_setup();
    timer8_setup();
    timer1_setup();
    GPIO_setup();

    timer_set_oc_value(TIM1, TIM_OC1, 220);
    //timer_set_oc_value(TIM1, TIM_OC2, 2500);
    //timer_set_oc_value(TIM1, TIM_OC3, 2500);

    timer_set_oc_value(TIM8, TIM_OC4, 1000);

    while(1) {
        //tim1_val = timer_get_counter(TIM1);
        //tim8_val = timer_get_counter(TIM1);
        //testvar = timer_get_counter(TIM8) - timer_get_counter(TIM1);
        
        if(timer_get_counter(TIM8)>2500) {
            gpio_set(SpiEncoderSCK_Port, SpiEncoderSCK_Pin);
        }
        else
        {
            gpio_clear(SpiEncoderSCK_Port, SpiEncoderSCK_Pin);
        }
        
    }

    //TIM_EGR(TIM1) |= TIM_EGR_BG;
    /*
    while(1){
        if(testvar==0) {
            timer_set_oc_value(TIM1, TIM_OC1, 500);
            gpio_set(DcLinkVoltage_Port, DcLinkVoltage_Pin);
            testvar=1;
        }
        else {
            timer_set_oc_value(TIM1, TIM_OC1, 42);
            gpio_clear(DcLinkVoltage_Port, DcLinkVoltage_Pin);
            testvar=0;
        }
        for (i = 0; i < 10000; i++) {
			__asm__("nop");
		}
    }
    */
    /*
    while(1) {
        gpio_toggle(DcLinkVoltage_Port, DcLinkVoltage_Pin);
		for (i = 0; i < 5; i++) {
			__asm__("nop");
		}
    */
    
}

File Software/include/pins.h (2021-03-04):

/*
 * This file is part of the CaroFoc project.
 */

#include <libopencm3/stm32/gpio.h>

#define DcLinkVoltage_Pin GPIO1
#define DcLinkVoltage_Port GPIOB
#define SpiEncoderNSS_Pin GPIO4
#define SpiEncoderNSS_Port GPIOA
#define SpiEncoderNSS2_Pin GPIO9
#define SpiEncoderNSS2_Port GPIOC
#define SpiEncoderSCK_Pin GPIO5
#define SpiEncoderSCK_Port GPIOA
#define SpiEncoderMISO_Pin GPIO6
#define SpiEncoderMISO_Port GPIOA
#define SpiEncoderMOSI_Pin GPIO7
#define SpiEncoderMOSI_Port GPIOA
#define CurrentU_Pin GPIO2
#define CurrentU_Port GPIOC
#define CurrentV_Pin GPIO1
#define CurrentV_Port GPIOC
#define CurrentW_Pin GPIO0
#define CurrentW_Port GPIOC
#define Gate_U_H_Pin GPIO8
#define Gate_U_H_Port GPIOA
#define Gate_V_H_Pin GPIO9
#define Gate_V_H_Port GPIOA
#define Gate_W_H_Pin GPIO10
#define Gate_W_H_Port GPIOA
#define Gate_U_L_Pin GPIO13
#define Gate_U_L_Port GPIOB
#define Gate_V_L_Pin GPIO14
#define Gate_V_L_Port GPIOB
#define Gate_W_L_Pin GPIO15
#define Gate_W_L_Port GPIOB
#define GateEnable_Pin GPIO3
#define GateEnable_Port GPIOB
#define CanRx_PIN GPIO8
#define CanRx_Port GPIOB
#define CanTx_PIN GPIO9
#define CanTx_Port GPIOB
#define GateErr1_Pin GPIO4
#define GateErr1_Port GPIOB
#define GateErr2_Pin GPIO5
#define GateErr2_Port GPIOB

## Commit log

2019-01-14 Some more layout work
    [AS5047D.sch, Can.sch, CaroFocIw.kicad_pcb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]
2019-01-14 Added DcLinkVoltageSensing, fixad a bug in schematic, routed remaining nets, got rid of all ERC and DRC errors and changed some mechanical aspects
    [AS5047D.sch, Can.sch, CaroFocIw.kicad_pcb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]
2019-01-15 Bugfix: placement of one board-to-board connector for current sensing phase U was not aligned with other board. Lots of layout refinements including lower inductance gate switching path, better groun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
    [CaroFocIw.kicad_pcb, CaroFocIw.sch, GateDriver.sch]
2019-01-16 Changed footprint of one inductor, rerouted microcontroller part. Mounting hole placement still needs some thoughts...
    [CaroFocIw.kicad_pcb, HalfBridge.sch, TPS560430X3F.sch]
2019-02-01 More capacitors, no airwires left (old form factor)
    [AS5047D.sch, Can.sch, CaroFocIw.kicad_pcb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]
2019-02-04 Smaller form factor -> lots of rerouting needed. Moved gate driver to PCB A
    [AS5047D.sch, Can.sch, CaroFocIw.kicad_pcb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]
2019-02-05 Some more routing, PCB B almost finished
    [CaroFocIw.kicad_pcb, CaroFocIw.sch, CurrentSensing.sch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]
2019-02-28 more layout
    [CaroFocIw.kicad_pcb]
2019-09-07 more routing
    [AS5047D.sch, Can.sch, CaroFocIw.kicad_pcb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]
2019-09-09 Routing (seems to be) done, should be reviewed before production
    [CaroFocIw.kicad_pcb]
2019-09-09 forgot to save
    [CaroFocIw.kicad_pcb, DcLinkCapacitors.sch, HalfBridge.sch]
2019-09-12 routing done, some via stitching and panelizing to do
    [CaroFocIw.kicad_pcb]
2019-09-12 some panelizing
    [CaroFocIw.kicad_pcb]
2019-10-01 preliminary version 1.0
    [AS5047D.sch, Can.sch, CaroFocIw.kicad_pcb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]
2019-10-03 actual version 1.0, several bugfixes and improvements
    [AS5047D.sch, CaroFocIw.kicad_pcb, CaroFocIw.sch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]
2019-10-07 Actual actual version 1.0, some minor changes. PCBs ordered.
    [CaroFocIw.kicad_pcb, PcbToPcbConnector.sch, STM32F4_64LQFP.sch]
2019-12-07 added some MCAD files
    [AnotherTry.FCStd, AnotherTryPCB.FCStd, BackPlateMotor.FCStd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]
2020-12-17 bom updated to include traces for debugging
2020-12-19 Added instructions for PCB assembly and first tests
2021-02-22 initial commit of new firmware
    [MagnetHolderD3.4L4.5.FCStd, MagnetHolderD3.5L5.0.FCStd, MagnetHolderD3.6L5.5.FCStd]
2021-02-25 timer 8 init added
2021-02-27 Timer 1 configured and working
2021-02-28 timer 8 configured to run in sync with timer 1
2021-03-04 timers 1 and 8 runnding in sync and 8 generating NCS pulses
